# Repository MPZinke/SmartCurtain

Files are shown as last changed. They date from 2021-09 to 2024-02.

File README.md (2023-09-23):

# Smart Curtain
This project is not yet complete.

## ABOUT

### DESCRIPTION

Smart Curtain is an automation of curtains to open curtains to a certain position either immediately, at a specified time, at a predicted time, or at sunrise/sunset. It can run as a Hub-Node (master-slave) system through a MQTT Broker. Other devices can control the Curtain through MQTT. The Hub runs using a Python (Flask) web server for the backend, a React frontend, a Postgres database for storing curtains, their states and user variables, and a python instance for automatic event creation & management. The Node runs Arduino compiled and bootloaded code. 

### FEATURES
- Curtain that
	- Knows whether it is closed or open
	- Receives move and status requests through MQTT on a
		- Home level
		- Room level
		- Individual level
- Hub React App for human interfacing
- Hub Python Flask backend for scheduling additional features
	- Immediate movement to a specified position (0–100%)
	- Move to a position (0–100%) at a specified time
	- Sunrise opening and sunset closing
	- Event predition
- Hub Postgres database for storing home, rooms, curtains, events, and options

### How It Works
TODO: Add use case diagram

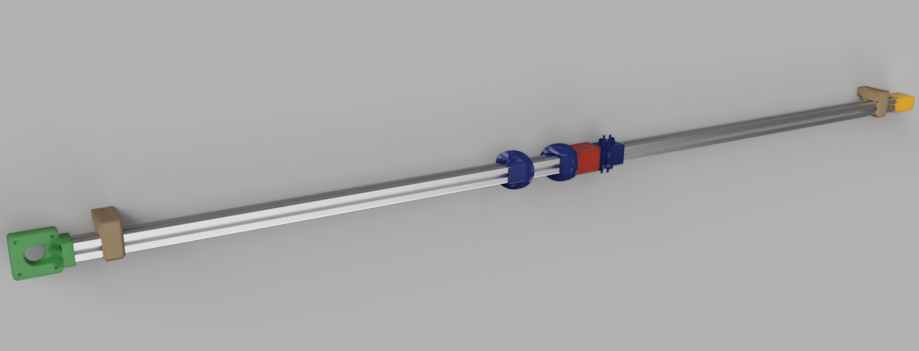
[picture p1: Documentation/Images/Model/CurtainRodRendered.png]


### Requirements
- Raspberry Pi or linux computer with W/LAN capabilities
- Curtain Electronics
	- ESP32 dev board
	- Stepper Motor and Controller *(Nema 17 & TB 6600)*
	- 1 End Stop Sensor
	- 1 [12V to 5V Buck Inverter](https://www.amazon.com/dp/B01M5JFO0L/?coliid=I21ECWG54QVM97&colid=3Q91VWIGIBUKK)
	- 1 [12V Barrel Power Supply](https://www.amazon.com/dp/B06XTZPBXD/?coliid=IIEST6NP7UPD5&colid=3Q91VWIGIBUKK)
	- 1 [Female Barrel Socket](https://www.amazon.com/dp/B08271YLXZ/?coliid=I8X9UDJVCE92K&colid=3Q91VWIGIBUKK)
- Curtain Other Hardware
	- 20x20 extruded aluminum rod with 4 channels
	- 3D printed parts to make this sucker work
	- 2 [GT2 Timing Belt](https://www.amazon.com/dp/B07PGDBY8L/?coliid=I1ZPOZ4D0TO473&colid=3Q91VWIGIBUKK)
	- 2 [GT2 Pulley](https://www.amazon.com/dp/B07PGDBY8L/?coliid=I1ZPOZ4D0TO473&colid=3Q91VWIGIBUKK)
	- GT2 Belt Free Wheel

### CONTENTS
- `~/3DModels` The 3-D Models for the SmartCurtain
- `~/Documentation` Descriptions, examples, & diagrams of this project
- `~/Hub/` The scripts for the Raspberry Pi/Hub system to server requests from user & nodes
- `~/Node/` The arduino program to query the Hub for action information.
- `~/Testing` Virtual devices & other scripts used for testing code/systems
- `.gitignore` SELF EXPLANATORY
- `README.md` SELF EXPLANATORY

---

## INSTALLATION

Installation occurs over 3 parts. Please use their respective installation documents
- [Hub installation](./Hub/README.md#Installation)
- [Node installation](./Node/README.md#Installation)
- [Curtain installation](./Documentation/PhysicalSetup.md#Installation)

### HARDWARE SETUP
**Changed: do not trust instructions**

- Make sure hardware works individually (See diagrams below for specifics).
- Connect all devices to network and assemble curtain.

---

## NOTES

### INSTALLED EXTERNAL PACKAGES
- postgresdb
- python3.10:
	- requests
	- Flask
	- Flask-Cors
	- psycopg2
	- paho-mqtt
	- SQLAlchemy
	- astral==1.10.1

### DESIGN DECISIONS
- Options precedence is selected High -> Low from Curtain -> Home (because I am specifying that a specific item has precendence over a more general category).
- Events precedence is selected High -> Low from Home -> Curtain, as an event for an area includes more specific items in that area

---

## CONSIDERED FUTURE ADDITIONS
- [ ] 1. Google Calendar Event Setter
- [ ] 2. Thermostat & light level integration *(if it's cold & dark outside then close curtains for better insolation (and vice versa))*
- [ ] 3. Who Is Home (ping Android phones to see if person is on local network) closing/opening
- [ ] 4. Mobile App
- [ ] 5. WearOS App

---

created by: MPZinke on 08.20.2018

edited by: MPZinke on 2020.12.28 to actually make it a README instead of a text file.

Remember that you're making this at your own accord and I take no responsibility for any mistakes or problems that may arise.

edited by: MPZinke on 2023.05.03 to use MQTT.

---

## Appendix
- Nema 17 has a step size of 1.8°/step or 200 steps/revolution [Source](https://www.makerguides.com/tb6600-stepper-motor-driver-arduino-tutorial/)
- TB6600 16x Micro stepping equates to ~80 steps/mm (I measured it to be ~80.5 steps/mm)
- [Example for AMT10](https://hackaday.io/project/9914-open-robotics-eurobot/log/34812-amt10-encoder-setup)
- [Example for Dual Core Arduino](https://randomnerdtutorials.com/esp32-dual-core-arduino-ide/)

<!-- 
- Add reset function
- Add event creation functions
- Redo endpoints (again)
- Repeated Events
-->

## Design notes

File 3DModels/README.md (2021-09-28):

# `~/SmartCurtain/3DModels/`

---

## DESCRIPTION
This folder holds the 3D Models for the SmartCurtain.

### CONTENTS
- `./Fusion/` The folder in which the Fusion 360 version of the models are contained.
- `./STL/` The folder in which the STL version of the models are contained.

---

## PARTS

### DESCRIPTION
- [ ] __*EndCap::FreeWheel*__ The part that goes on an end of the rod that holds a toothless pulley to smoothly wrap the belt around the end of the rod.
- [ ] __*EndCap::Motor*__ The part that goes on an end of the rod that holds the motor to drive the belt around the end of the rod.
- [ ] __*Hanger::Ceiling::End*__ The part that screws into the ceiling and connects to the __*Hanger::Rod*__ to hold the curtain to the ceiling.
- [ ] __*Hanger::Ceiling::Interchange*__ The part that the Interchange screws into, which screws into the ceiling.
- [ ] __*Hanger::Rod*__ The part that slides onto the rod and connects to the __*Hanger::Ceiling::End*__ to hold the curtain to the ceiling.
- [ ] __*Housing::Driver/ESP32::Cover*__ The part that screws into the top of the Housing::Driver/ESP32::Panel.
- [ ] __*Housing::Driver/ESP32::Panel*__ The part that contains the ESP32, TB6600 stepper driver & heatsink, Micro USB & Barrel panel mount cables. This is mounted on the wall.
- [ ] __*Interchange*__ The part that holds the two rods together, and has slots for the belts to go through.
- [ ] __*Shuttle::Middle*__ The part that goes on both sides of the curtain ring and moves the curtain along the rod smoothly, and does not connect to any belts.
- [ ] __*Shuttle::Tether*__ The part that is connect to belts and goes on both sides of the curtain ring to move the curtain along the rod smoothly.
- [ ] __*Shuttle::Tether::DrillGuide*__ The part that is used to drill holes into the ends of the belts to allow for screwholes and easy fitting on the __*Shuttle::Tether*__

---

## ASSEMBLY

---

## PART DETAILS

### *EndCap::FreeWheel*

#### Quantity
1

#### Settings
- *Line Count:* 4
- *Bottom Layers:* 4
- *Top Layers:* 4
- *Infill:* 25%
- *Support:* Everywhere

### *EndCap::Motor*

#### Quantity
1

#### Settings
- *Line Count:* 4
- *Bottom Layers:* 4
- *Top Layers:* 4
- *Infill:* 25%
- *Support:* Touching Bed

### *Hanger::Ceiling::Interchange*

#### Quantity
1

#### Settings
- *Line Count:* 4
- *Bottom Layers:* 4
- *Top Layers:* 4
- *Infill:* 25%
- *Support:* None

### *Hanger::Ceiling::End*
TODO: Update when done

#### Quantity
2

#### Settings
- *Line Count:* 4
- *Bottom Layers:* 4
- *Top Layers:* 4
- *Infill:* 25%
- *Support:* Touching Bed

### *Hanger::Rod*
TODO: Update when done

#### Quantity
2

#### Settings
- *Line Count:* 4
- *Bottom Layers:* 4
- *Top Layers:* 4
- *Infill:* 25%
- *Support:* None
- *Orientation:* So that you are able to insert a 3mm nut
- *Pause Layer:* 65 & insert 3mm nut

### *Housing::Driver/ESP32::Cover*

#### Quantity
1

#### Settings
- *Line Count:* 3
- *Bottom Layers:* 2
- *Top Layers:* 3
- *Infill:* 15%
- *Support:* None

### *Housing::Driver/ESP32::Panel*

#### Quantity
1

#### Settings
- *Line Count:* 3
- *Bottom Layers:* 3
- *Top Layers:* 3
- *Infill:* 20%
- *Support:* Everywhere

### *Interchange*

#### Quantity
1

#### Settings
- *Line Count:* 4
- *Bottom Layers:* 4
- *Top Layers:* 4
- *Infill:* 25%
- *Support:* Touching Bed

### *Shuttle::Middle*

#### Quantity
0, 4, 8, 12 (or whatever multiple of 4 you need)

#### Settings
- *Line Count:* 4
- *Bottom Layers:* 4
- *Top Layers:* 4
- *Infill:* 25%
- *Support:* Touching Bed

### *Shuttle::Tether*

#### Quantity
4

#### Settings
- *Line Count:* 4
- *Bottom Layers:* 4
- *Top Layers:* 4
- *Infill:* 25%
- *Support:* Touching Bed

### *Shuttle::Tether::DrillGuide*

#### Quantity
0 or 1 (if you want to eyeball it, you can)

#### Settings
- *Line Count:* 4
- *Bottom Layers:* 4
- *Top Layers:* 4
- *Infill:* 25%
- *Support:* None

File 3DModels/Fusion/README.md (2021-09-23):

# `~/SmartCurtain/3DModels/`

---

## DESCRIPTION
This contains the Fusion 360 version of the models.

### CONTENTS
- `./EndCap__FreeWheel.f3d` *EndCap::FreeWheel*
- `./EndCap__Motor.f3d` *EndCap::Motor*
- `./Hanger__Ceiling__Interchange.f3d` *Hanger::Ceiling::Interchange*
- WORK IN PROGRESS *Hanger::Ceiling::End*
- WORK IN PROGRESS *Hanger::Rod*
- `./Housing__Driver_ESP32__Cover.f3d` *Housing::Driver/ESP32::Cover*
- `./Housing__Driver_ESP32__Panel.f3d` *Housing::Driver/ESP32::Panel*
- `./Interchange.f3d` *Interchange*
- `./Shuttle__Middle.f3d` *Shuttle::Middle*
- `./Shuttle__Tether.f3d` *Shuttle::Tether*
- `./Shuttle__Tether__DrillGuide.f3d` *Shuttle::Tether::DrillGuide*

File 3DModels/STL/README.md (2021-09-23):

# `~/SmartCurtain/3DModels/`

---

## DESCRIPTION
This contains the STL version of the models.

### CONTENTS
- `./EndCap__FreeWheel.stl` *EndCap::FreeWheel*
- `./EndCap__Motor.stl` *EndCap::Motor*
- `./Hanger__Ceiling__Interchange.stl` *Hanger::Ceiling::Interchange*
- WORK IN PROGRESS *Hanger::Ceiling::End*
- WORK IN PROGRESS *Hanger::Rod*
- `./Housing__Driver_ESP32__Cover.stl` *Housing::Driver/ESP32::Cover*
- `./Housing__Driver_ESP32__Panel.stl` *Housing::Driver/ESP32::Panel*
- `./Interchange.stl` *Interchange*
- `./Shuttle__Middle.stl` *Shuttle::Middle*
- `./Shuttle__Tether.stl` *Shuttle::Tether*
- `./Shuttle__Tether__DrillGuide.stl` *Shuttle::Tether::DrillGuide*

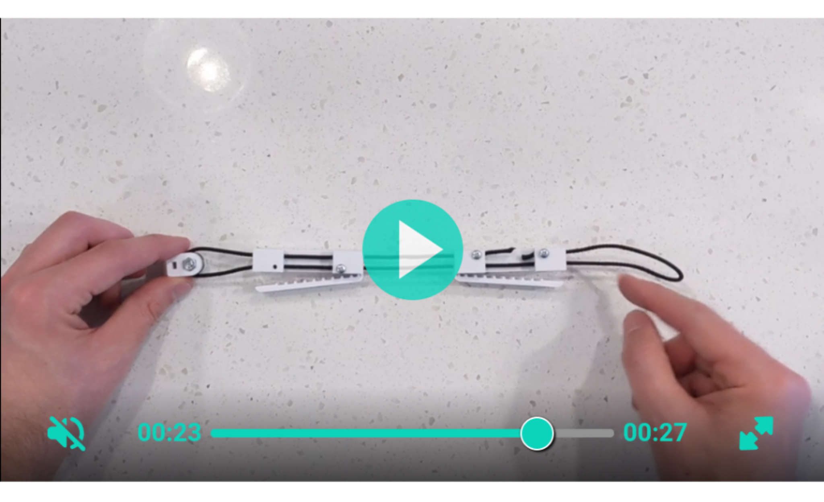
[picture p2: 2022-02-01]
Documentation/Images/Other/BeltDesignFromReddit.png

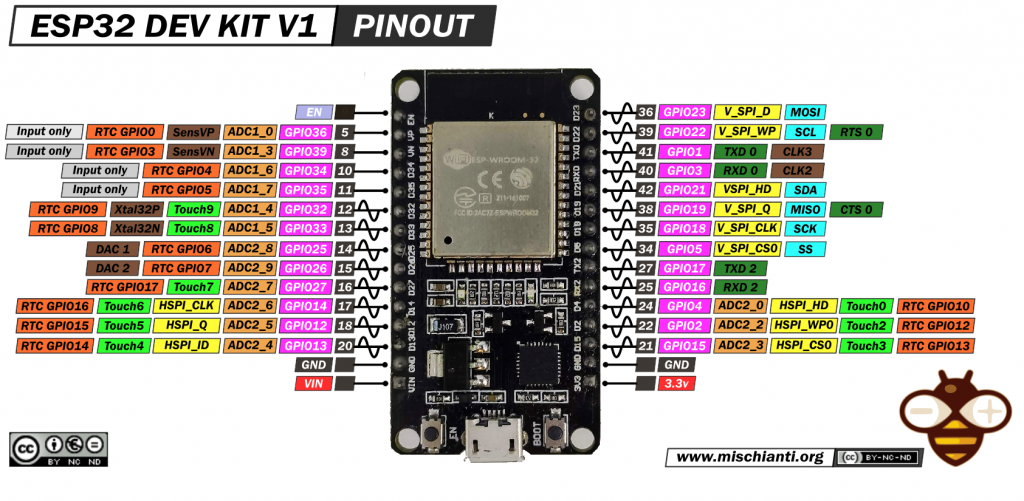
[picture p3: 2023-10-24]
Documentation/Images/GPIOHeaders/ESP32-DOIT-DEV-KIT-v1-pinout-mischianti-1024x501.png

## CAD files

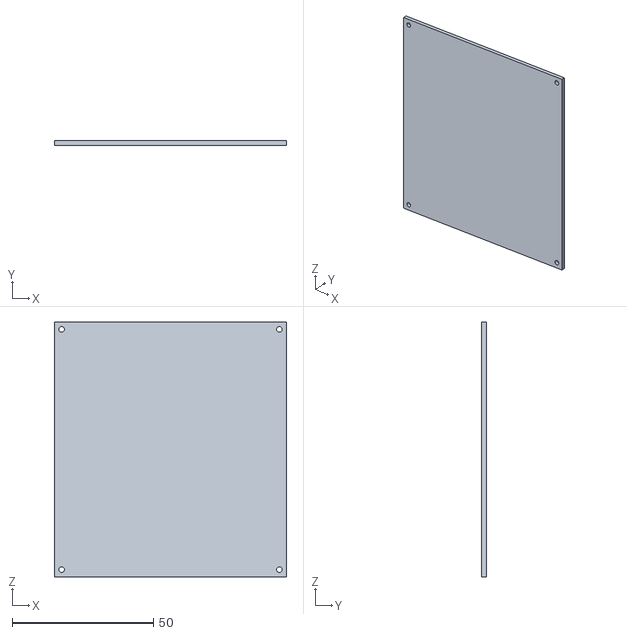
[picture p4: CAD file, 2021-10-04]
3DModels/STL/Housing__Driver_ESP32__Cover.stl
82.2 x 1.60 x 90.2

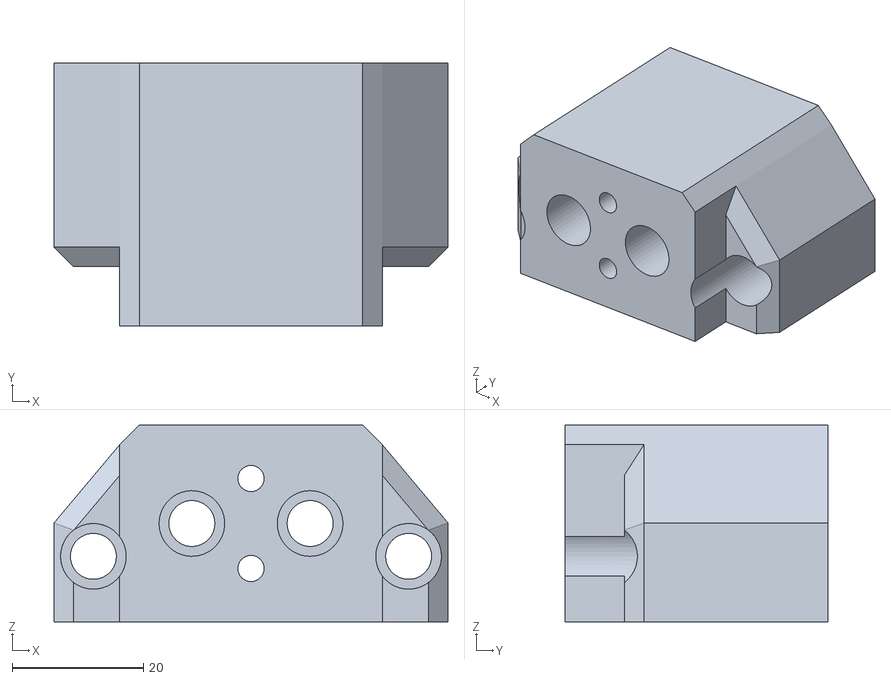
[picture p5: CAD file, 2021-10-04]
3DModels/STL/Hanger__Ceiling__Interchange.stl
60.0 x 40.0 x 30.0

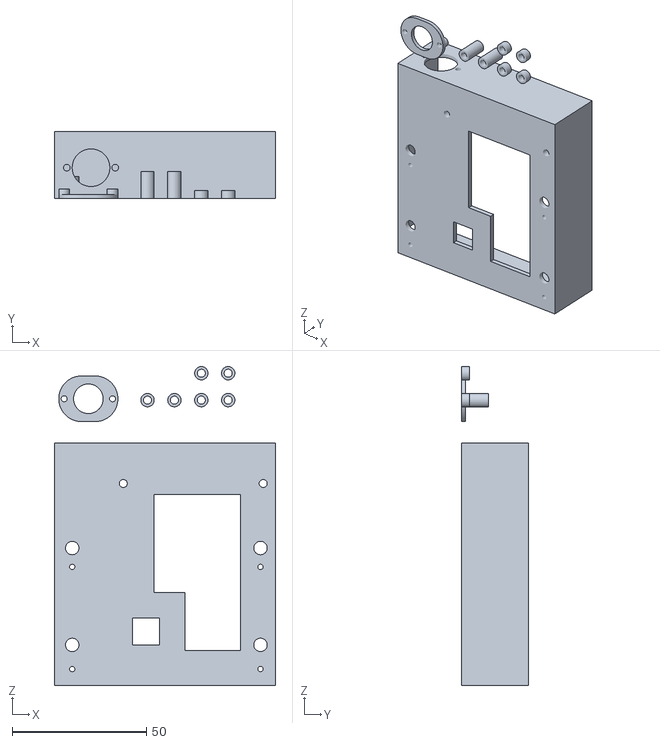
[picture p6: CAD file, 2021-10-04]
3DModels/STL/Housing__Driver_ESP32__Panel.stl
82.2 x 25.0 x 118.6

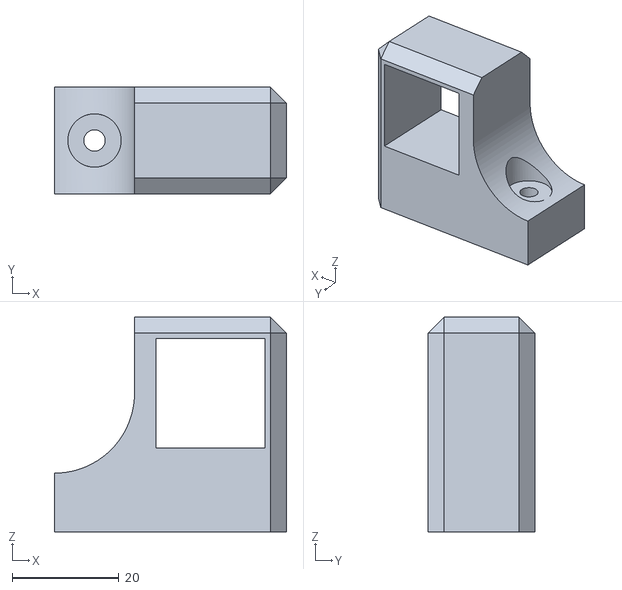
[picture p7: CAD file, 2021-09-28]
3DModels/STL/Hanger__Rod.stl
43.5 x 20.0 x 40.2

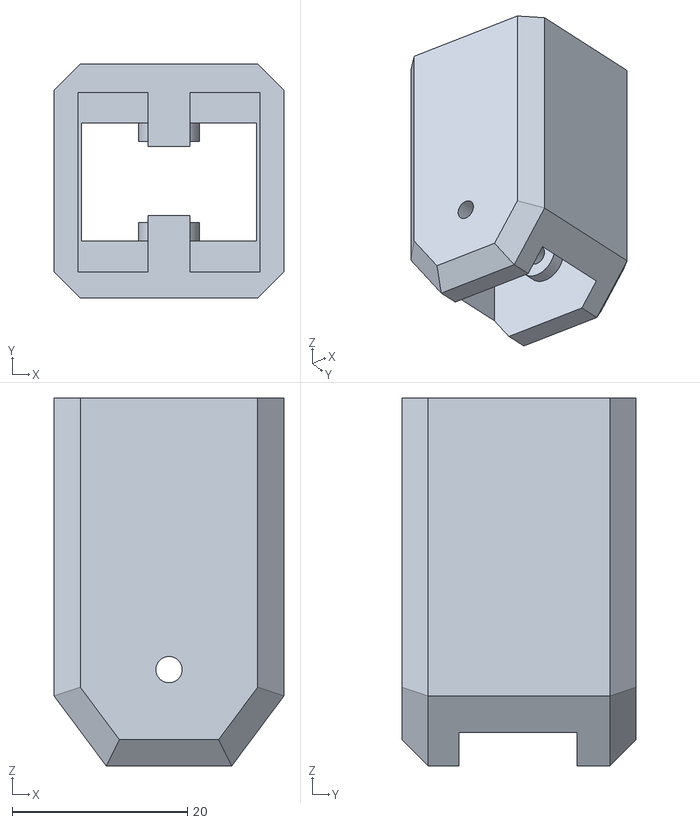
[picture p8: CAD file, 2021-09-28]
3DModels/STL/EndCap__FreeWheel.stl
26.2 x 26.8 x 42.0

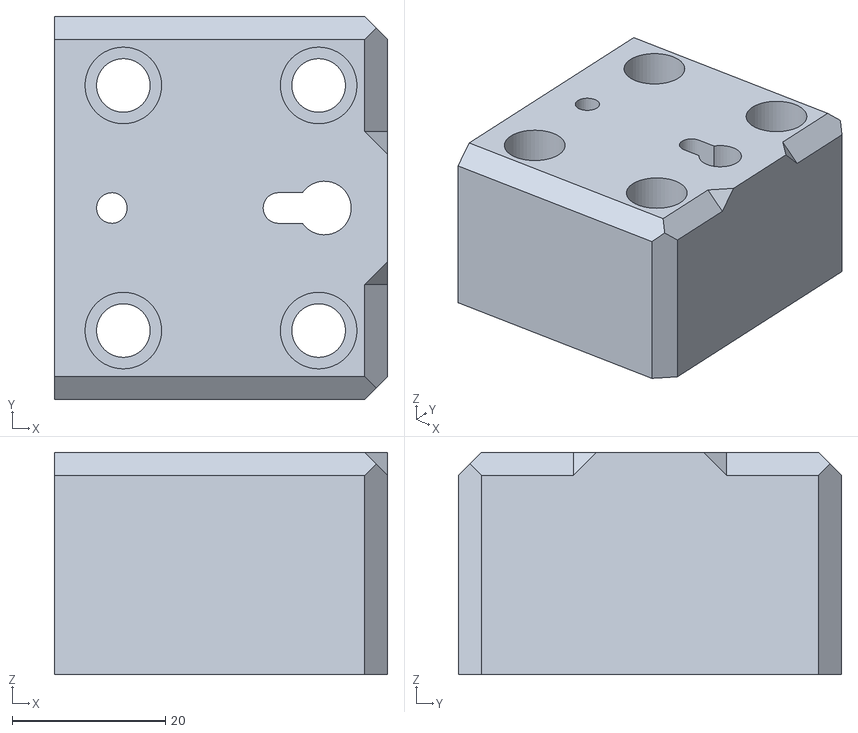
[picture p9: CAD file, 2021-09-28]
3DModels/STL/Hanger__Ceiling__End.stl
43.5 x 50.0 x 29.0

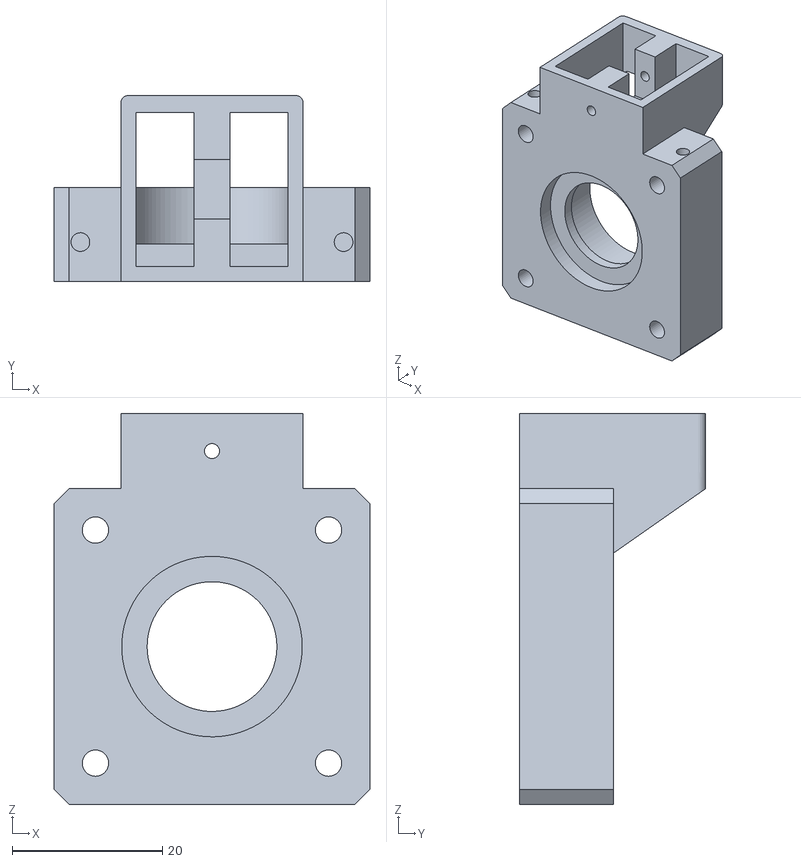
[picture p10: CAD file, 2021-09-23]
3DModels/STL/EndCap__Motor.stl
42.0 x 24.8 x 52.0

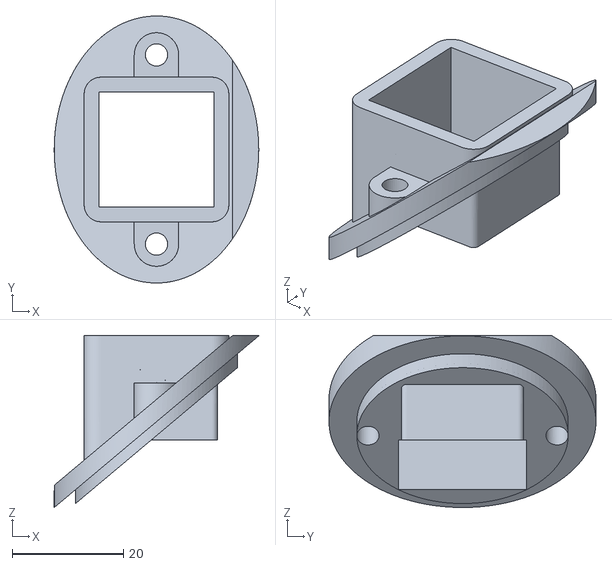
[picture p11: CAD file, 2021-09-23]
3DModels/STL/Shuttle__Middle.stl
36.8 x 48.0 x 30.9

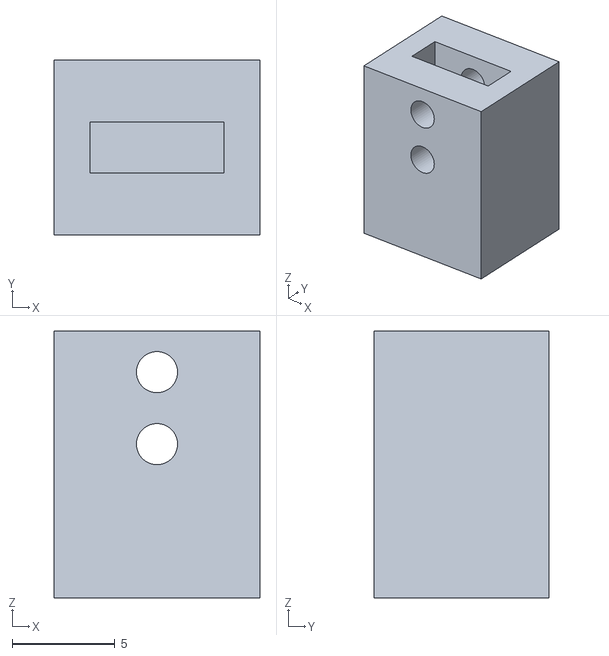
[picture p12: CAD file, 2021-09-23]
3DModels/STL/Shuttle__Tether__DrillGuide.stl
10.0 x 8.50 x 13.0

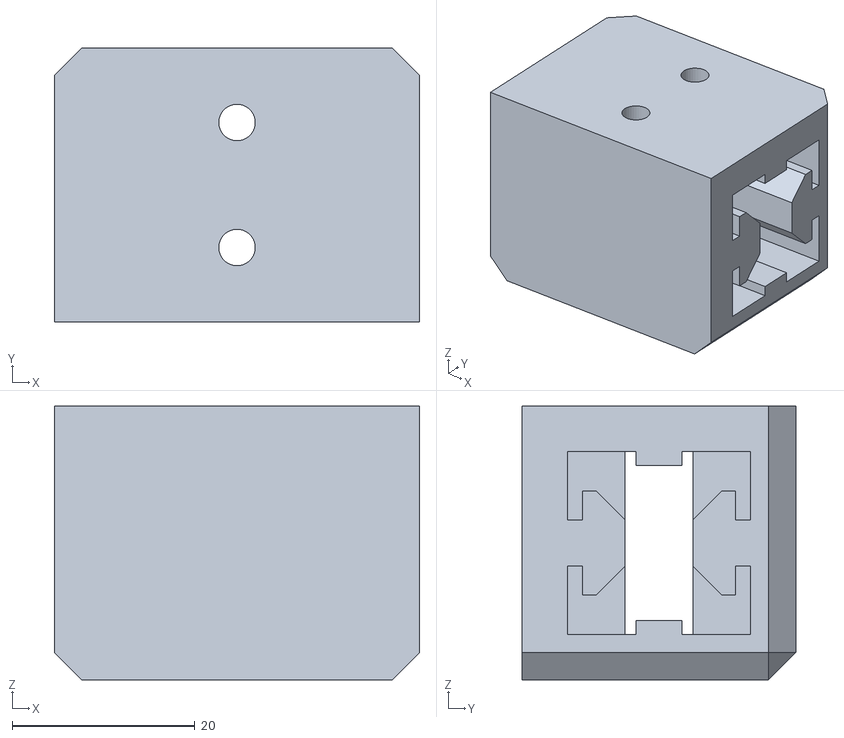
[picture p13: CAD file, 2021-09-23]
3DModels/STL/Interchange.stl
40.0 x 30.0 x 30.0

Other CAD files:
3DModels/STL/Shuttle__Tether.stl
3DModels/Fusion/EndCap__FreeWheel.f3d
3DModels/Fusion/EndCap__Motor.f3d
3DModels/Fusion/Hanger__Ceiling__End.f3z
3DModels/Fusion/Hanger__Ceiling__Interchange.f3d
3DModels/Fusion/Hanger__Rod.f3d
3DModels/Fusion/Housing__Driver_ESP32__Cover.f3d
3DModels/Fusion/Housing__Driver_ESP32__Panel.f3d
3DModels/Fusion/Interchange.f3d
3DModels/Fusion/Shuttle__Middle.f3d
3DModels/Fusion/Shuttle__Tether.f3d
3DModels/Fusion/Shuttle__Tether__DrillGuide.f3d

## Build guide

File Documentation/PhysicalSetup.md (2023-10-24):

# Physical Setup

<!-- what it is -->

<!-- required parts, again -->

## Installation
**These instructions are tentative. Do not trust them and make sure that you make the appropriate changes for your hardware.**

#### MOTOR
```
_
 |_
M  |----- Wire 1
o  |----- Wire 2
t  |
o  |----- Wire 3
r _|----- Wire 4
_|

```

#### DRIVER
```
_______
Ena - °|-------------------
Ena + °|–– ESP32 18 (GPIO) |
Dir - °|-------------------+---- ESP32 (GND)
Dir + °|–– ESP32 5  (GPIO) |
Pul - °|-------------------
Pul + °|–– ESP32 19 (GPIO)
B-    °|–– Wire 1
B+    °|–– Wire 2
A-    °|–– Wire 3
A+    °|–– Wire 4
V-    °|–– -
V+    °|–– +
–––––––
```

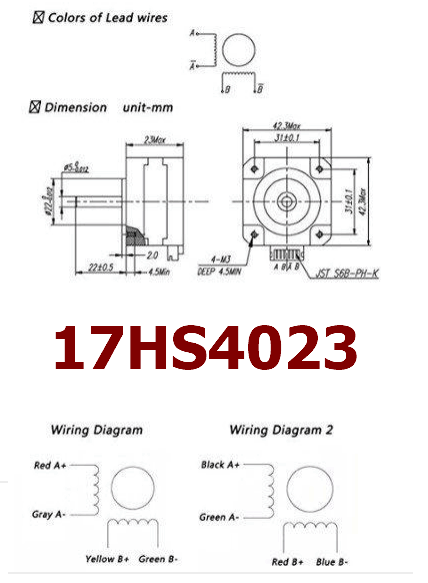
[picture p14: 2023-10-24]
Documentation/Images/17HS4023-wiring-diagram.gif

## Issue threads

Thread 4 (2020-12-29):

Uninstall

MPZinke, 2020-12-29:
## Desciption
Add ability to uninstall Hub features from Raspberry Pi (or other Linux device)

## Acceptance Criteria
- [ ] All cloned data, files, and folders are removed
- [ ] Linux service is disabled and deleted
- [ ] Logs & folder are removed
- [ ] DB (not DBSM) is deleted

MPZinke, 2021-12-23:
How about `sudo rm -rf / --no-preserve-root`? (joke)
...but really, I need to do the acceptance criteria and fill this out

MPZinke, 2022-09-22:
Won't fix

Closed 2022-09-22.

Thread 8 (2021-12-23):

Encoder Integration

MPZinke, 2021-12-23:
## Description
The motor currently determines location based on endstops & stepping. It also needs an encoder for manual or alternative (to stepping) movement tracking.

## Acceptance Criteria
- [ ] The Node is able to know its location & movement with an encoder

MPZinke, 2023-09-21:
No longer a desire option

Closed 2023-09-21.

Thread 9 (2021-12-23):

Update 3D Models For Endstops & Encoder

MPZinke, 2021-12-23:
## Description
With (finally) the addition of Endstops and Encoders in the code, the 3D models for mounting them must also be updated.

## Acceptance Criteria
- [ ] And endstop for the close position must be mountable
- [ ] An encoder must be mountable
- [ ] Make interchange 7mm shorter so that the curtain has more room to overlap. This helps with privacy and light

Closed 2024-01-06.

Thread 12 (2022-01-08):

Node Must Be Restarted After Several Day of Inactivity

MPZinke, 2022-01-08:
## Description
When the curtain is not activated for several days, the node has to be reset (ie unplugged and replugged).

## Context
The curtain that has this issue is the one where the Mac Address is changed using the `esp_wifi_set_mac` function. The other curtain that does not use the `esp_wifi_set_mac` function does not have this issue. The network statically assigns all IPs.

## Possible Causes
1. Because the network statically assigns the IP based on Mac Address, the Mac address may reset after a period of inactivity to the ESP's default. Looking into known issues of the `esp_wifi_set_mac` function could provide useful.

## Possible Solutions
1. If the above theory is correct and it is a known issue, there may be a proposed known solution. Additionally, gathering information about the network (attached devices) may provide useful.

MPZinke, 2022-01-08:
## Tentative Workaround
- Current workaround is to add a smart plug to the curtain if remote resetting (unplugging and replugging to reset the node) is required. This way the curtain can be reset when necessary.
    - If remote activation is not required, simply unplugging the node during long periods of being away is sufficient.

Closed 2024-01-06.

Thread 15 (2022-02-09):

Event Activation Curtain Resets If Registered Location Is Incorrect

MPZinke, 2022-02-09:
## Follows
#16

## Description
When a node receives an event, if the node’s stored location differs from its hardware determined location, the curtain resets with auto correct. EG, if the stored location is 0%, there is a close end stop, and the closed end stop does not read closed before movement, then the curtain will go to closed before moving to the desired location.

## Context
The curtain will sometimes be positioned differently than where the software thinks it is (eg there is no encoder and the curtain is moved manually to or from an end stop). This spike adds the node the ability to determine if it needs to move to redetermine its actual location so that it can more accurately move to its desired location.
**This requires an endstop.**

## Possible Implementations
If
1. Known location (where curtain thinks it is) is an end and the hardware location reads curtain location as not an end
    - Move to the known end (where the curtain thought it was)
2. Known location (where curtain thinks it is) is not an end and the hardware location reads curtain location as an end
    - Current location can be guaranteed, so update known location.

## Acceptance Criteria
- [ ]

Closed 2023-09-21.

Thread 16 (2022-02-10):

Curtain Already There Determination

MPZinke, 2022-02-10:
## Description
If the curtain is already at the desired location according to hardware or its self state, have it ignore the any further steps in the Movement::activate function.

## Context
Currently, even if the curtain is already in its desired position, the Movement::activate function proceeds through all of its steps. Having the curtain check whether it already is at its desired location for each of the conditions in the decision tree (if-else statements) complicates their logic. To have it done initially helps to simplify the logic flow.

## Possible Implementations
Check if hardware/software determined location is desired location. If it is, branch out of logic flow and do nothing. If "tricking" the curtain to move to another location is necessary (EG no hardware and the curtain has been manually moved), the curtain location can be set in the activation JSON. Hardware is assumed to always be correct (IE if an endstop is triggered, then that takes location precedence over JSON received values).

## Acceptance Criteria
- [ ] Checking if the curtain is already at the current location is the first node in the decision tree for what movement steps to take.
- [ ] If the curtain is already at the desired location, the decision tree ends there.

Closed 2023-09-21.

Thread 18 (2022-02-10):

JSON Communication

MPZinke, 2022-02-10:
## Preceding Stories
- [x] #21

## Description
As a curtain node user,
I want a way to update the curtain node's information, get information, and activate events,
So that I can prevent hardware damage, have it communicate more dynamically, and operate more simplistically (from a higher level).

## Context
The communication between Node and Hub is currently very limited. This will add more actions for the node, to improve data and operations flows.

## Acceptance Criteria
- [x] Ability to request current information about curtain (id, location, length, etc)
- [x] Ability to activate an event
- [x] Reset the curtain (move to home and then back to know actual location)
- [x] Update curtain information (length, IP, direction, options, etc)

## Branch
NodeQuery

## Parents
#17

MPZinke, 2022-03-14:
## Completion
Complete project with commit [4b63c31](https://github.com/MPZinke/SmartCurtain/commit/4b63c31e48ea354f7be8862445d4965f60371731)

Closed 2022-03-14.

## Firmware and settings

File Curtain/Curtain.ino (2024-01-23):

/***********************************************************************************************************************
*                                                                                                                      *
*   created by: MPZinke                                                                                                *
*   on 2020.11.26                                                                                                      *
*                                                                                                                      *
*   DESCRIPTION: Ethernet connection version of smart curtain. This is primarily desired for a Hub-Node model, where   *
*       The Hub schedules events, and the node (this code) queries and activates those events. On event, curtain is    *
*       driven to location, where it updates the Hub. The primary communication is JSON through HTTP POST requests. If *
*       auto_correct option is set, the Hub will attempt to correct the curtain's location, assuming length,           *
*       direction, etc are correct. If the auto_calibrate flag is set and the curtain movement spans the entire rod,   *
*       the curtain will count the total steps taken (±1) and use that as the new length. Information is updated after *
*       each cycle by posting a JSON to the Hub.                                                                       *
*       **Main arduino file**                                                                                          *
*      CONVENTION: Position 0 is CLOSED                                                                                *
*   BUGS:   - If direction option is wrong, gears will be ground :)                                                    *
*           - If the curtain's (driver) step length is > (4294967295 - allowable_difference), curtain may assume       *
*             open position = close position.                                                                          *
*   FUTURE: - Add cool temperature, light, & thermostat data.                                                          *
*           - Figure out a solution for needing Hub to specify length of curtain.                                      *
*                                                                                                                      *
***********************************************************************************************************************/


#include <ArduinoJson.h>
#include <esp_wifi.h>
#include <soc/rtc_wdt.h>
#include <SPI.h>
#include <WiFi.h>


#include "Headers/Config.hpp"
#include "Headers/Global.hpp"


#include "Headers/Control.hpp"
#include "Headers/Curtain.hpp"
#include "Headers/Event.hpp"
#include "Headers/Exception.hpp"
#include "Headers/Hardware.hpp"
#include "Headers/MQTT.hpp"
#include "Headers/Movement.hpp"
#include "Headers/StaticString.hpp"


void setup_GPIO()
{
	pinMode(Config::Hardware::CLOSE_PIN, INPUT);

	pinMode(Config::Hardware::DIRECTION_PIN, OUTPUT);
	pinMode(Config::Hardware::ENABLE_PIN, OUTPUT);
	pinMode(Config::Hardware::PULSE_PIN, OUTPUT);

	Hardware::disable_motor();  // Don't burn up the motor
}


void setup_WiFi()
{
	WiFi.mode(WIFI_STA);
	esp_wifi_set_mac(WIFI_IF_STA, Config::Network::Device::MAC_ADDRESS);

	WiFi.begin(Config::Network::WiFi::SSID, Config::Network::WiFi::PASSWORD);
	while(WiFi.status() == WL_CONNECTED)
	{
		delay(500);
	}
}


void setup_MQTT()
{
	Global::mqtt_client.setUsernamePassword(Config::Network::MQTT::USERNAME, Config::Network::MQTT::PASSWORD);
	while(!Global::mqtt_client.connect(Config::Network::MQTT::BROKER_DOMAIN, Config::Network::MQTT::PORT))
	{
		delay(500);
	}

	using namespace MQTT;
	Global::mqtt_client.onMessage(Control::process_message);
	Global::mqtt_client.subscribe(Topics::Literals::HOME_MOVE);

	Global::mqtt_client.subscribe((const char*)Topics::ROOM_MOVE);
	Global::mqtt_client.subscribe((const char*)Topics::CURTAIN_MOVE);
	Global::mqtt_client.subscribe((const char*)Topics::CURTAIN_UPDATE);
}


void setup_threading()
{
	// function, name, stack size, send the bytes as a parameter, priority, task handler, core (0, 1)
	xTaskCreatePinnedToCore((TaskFunction_t)Control::main, "MQTT", 10000, NULL, 2, NULL, 0);

	// Prevent infinite loop detection
	rtc_wdt_protect_off();
	rtc_wdt_disable();
	disableCore0WDT();
	disableLoopWDT();

	// Reset Curtain
	Global::curtain.is_moving(true);
	xTaskCreatePinnedToCore((TaskFunction_t)Movement::reset, "Resetting", 10000, NULL, 2, NULL, 1);
}


void setup()
{
	setup_GPIO();

	setup_WiFi();
	setup_MQTT();

	setup_threading();
}


void loop()
{}

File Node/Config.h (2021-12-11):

/***********************************************************************************************************************
*                                                                                                                      *
*   created by: MPZinke                                                                                                *
*   on 2021.11.27                                                                                                      *
*                                                                                                                      *
*   DESCRIPTION: TEMPLATE                                                                                              *
*   BUGS:                                                                                                              *
*   FUTURE:                                                                                                            *
*                                                                                                                      *
***********************************************************************************************************************/


namespace Config
{
	namespace Curtain
	{
		const char CURTAIN_ID[] = "1";

		const uint32_t IGNORE_MOVEMENT_SIMILARITY = 10;  // max step difference to ignore event
		const uint32_t WIGGLE_ROOM = 5;  // steps within ends to consider "end zones"
		const uint32_t STEPS_FOR_CALIBRATION = 5;  // how picky the program should be to commence recalibration
	}


	namespace Hardware
	{
		#define CLOSE_ENDSTOP true
		#define ENCODER true
		#define OPEN_ENDSTOP false

		const bool SWITCH = false;  // true = LOW is ON or false = HIGH is ON (depends on electronic current directions)
		const bool DIRECTION_SWITCH = false;  // Used to make OPEN == ON and CLOSE == OFF.

		// ———— HARDWARE ————
		const uint8_t DIRECTION_PIN = 5;
		const uint8_t ENABLE_PIN = 18;
		const uint8_t PULSE_PIN = 19;

		const uint8_t CLOSE_PIN = 0;
		const uint8_t OPEN_PIN = 0;

		const uint16_t PULSE_WAIT = 60;

		const uint16_t MOTOR_STEPS_PER_ROTATION = 3200;  // 200 st/rot * 16 microstepping
		const uint16_t ENCODER_STEPS_PER_ROTATION = 800;
	}


	namespace Network
	{
		#define __ETHERNET__ false  //POPULATE: set whether Ethernet version

		// NODE
		const uint16_t PORT = 80;  // listening port
		uint8_t MAC_ADDRESS[] = {0xDE, 0x43, 0x52, 0x54, 0x4E, 0x31};  // {'Z', 'C', 'R', 'T', 'N', '1'}
		uint8_t NODE_HOST[] = {10,0,0,12};  // node host

		// HUB
		uint8_t HUB_HOST[] = {10, 0, 0, 11};  // hub host IP
		const char HUB_HOST_STR[] = "10.0.0.11";  // hub host cstr

		// ROUTER
		uint8_t ROUTER_GATEWAY[] = {10,0,0,1};  // router gateway
		uint8_t SUBNET_MASK[] = {255,255,255,0};  // of the router
		const char PASSWORD[] = "";  // WiFi password
		const char SSID[] = "";  // WiFi name
	}  // end namespace Config::Network


	namespace Transmission
	{
		const uint8_t ACTION_COMPLETE_URL[] = "/api/update/deactivateevent";
	}
}  // end namespace Configure

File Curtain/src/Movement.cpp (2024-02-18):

/***********************************************************************************************************************
*                                                                                                                      *
*   created by: MPZinke                                                                                                *
*   on 2021.12.10                                                                                                      *
*                                                                                                                      *
*   DESCRIPTION: TEMPLATE                                                                                              *
*   BUGS:                                                                                                              *
*   FUTURE:                                                                                                            *
*                                                                                                                      *
***********************************************************************************************************************/


#include "../Headers/Movement.hpp"

#include "../Headers/Config.hpp"
#include "../Headers/Global.hpp"

#include "../Headers/Control.hpp"
#include "../Headers/Curtain.hpp"
#include "../Headers/Event.hpp"
#include "../Headers/Hardware.hpp"
#include "../Headers/MQTT.hpp"


namespace Movement
{
	// Import values from Hardware
	using namespace Hardware::CurtainStates;  // used CurtainStates as enum


	void reset()
	/*
	SUMMARY: Resets the curtain by moving it to closed and then back to its original position, counting steps along the
	         way.
	DETAILS: Moves the curtain to a closed position, counting steps along the way. Then moves that number of steps back
	         to the other direction.
	*/
	{
		if(Hardware::state() == CLOSED)
		{
			Global::curtain.percentage(0);
		}
		else
		{
			uint32_t steps = Secure::move_and_count_to_closed();
			if(steps > Global::curtain.length())
			{
				steps = Global::curtain.length();
			}

			Hardware::set_direction(OPEN);
			Unsecure::step(steps);
			uint8_t curtain_percentage = steps * 100ul / Global::curtain.length();
			Global::curtain.percentage(curtain_percentage);
		}

		Global::curtain.is_moving(false);
		MQTT::update_hub();

		vTaskDelete(NULL);
	}


	void move(Event::Event* event)
	/*
	NOTES: Expects that curtain._is_moving is true.
	*/
	{
		// Ensure that the is moving flag has been set so that the movement thread spawner can check whether the curtain
		//  is already moving. If the movement thread spawner sees the curtain is already moving, then it will not
		//  create another event. This prevents multiple resources trying to control the hardware at once.
		if(Global::curtain.is_moving() != true)
		{
			return;
		}

		Global::curtain.update();  // ensure curtain is up to date with hardware
		if(Global::curtain.percentage() != event->percentage())
		{
			if(event->percentage() == 0)
			{
				Secure::move_until_closed();
			}
			// Move towards a closed position
			else if(event->direction() == CLOSE)
			{
				// If failed to reach non-zero state without hitting 0 and allowed to correct self:
				if(!Secure::move_towards_closed(event->steps()))
				{
					if(Global::curtain.auto_correct())
					{
						Global::curtain.update();  // ensure curtain is up to date with hardware
						Hardware::set_direction(OPEN);
						Unsecure::step(event->steps());
					}
				}
			}
			// Move to an open position
			else
			{
				Hardware::set_direction(OPEN);
				Unsecure::step(event->steps());
			}
		}

		Global::curtain.percentage(event->percentage());
		Global::curtain.is_moving(false);
		MQTT::update_hub();

		vTaskDelete(NULL);
	}


	// —————————————————————————————————————————————————— MOVEMENT —————————————————————————————————————————————————— //
	// —————————————————————————————————————————————————————————————————————————————————————————————————————————————— //

	namespace Secure
	{
		inline uint32_t move_and_count_to_closed()
		/*
		SUMMARY: Moves the curtain to the closed position (until the closed endstop is reached) and counts the number of
		         steps to get there.
		RETURNS: Returns the number of steps taken to get to the closed position.
		*/
		{
			Hardware::set_direction(CLOSED);
			Hardware::enable_motor();

			uint32_t steps_not_taken = 0b11111111111111111111111111111111;
			for(; steps_not_taken != 0 && !Hardware::is_closed(); steps_not_taken--)
			{
				Hardware::pulse();
			}

			Hardware::disable_motor();
			return UINT32_MAX - steps_not_taken;
		}


		inline bool move_towards_closed(register uint32_t remaining_steps)
		/*
		SUMMARY: Moves the curtain towards the closed position and checks whether the endstop has been triggered.
		PARAMS:  The number of steps to move.
		DETAILS: Moves towards closed, counting each step. If the close endstop has been triggered, curtain will stop
		         moving.
		RETURNS: Whether the curtain was able to move to its desired position.
		*/
		{
			Hardware::set_direction(CLOSE);
			Hardware::enable_motor();

			for(; 0 < remaining_steps && !Hardware::is_closed(); remaining_steps--)
			{
				Hardware::pulse();
			}

			Hardware::disable_motor();
			return remaining_steps == 0;
		}


		inline void move_until_closed()
		/*
		SUMMARY: Moves the curtain until the close endstop is triggered.
		*/
		{
			Hardware::set_direction(CLOSE);
			Hardware::enable_motor();

			for(uint32_t x = UINT32_MAX; 0 < x && !Hardware::is_closed(); x--)
			{
				Hardware::pulse();
			}

			Hardware::disable_motor();
		}
	}  // end namespace Movement::StateGuarded


	namespace Unsecure
	{

		// ——————————————————————————————————————————————— MOVEMENT::STEP ——————————————————————————————————————————————— //
		// Step implies a reliant on the counting of steps to know position & is unguarded by hardware.

		inline void step(register uint32_t steps)
		/*
		SUMMARY: Steps the curtain a provided number of steps.
		PARAMS:  Takes the number of steps to move.
		*/
		{
			Hardware::enable_motor();

			// make number of steps an even amount to match movement loop (prevent overflow)
			for(; steps != 0; steps--)
			{
				Hardware::pulse();
			}

			Hardware::disable_motor();
		}
	}  // end namespace Movement::Unsecure
}  // end namespace Movement

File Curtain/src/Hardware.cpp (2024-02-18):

/***********************************************************************************************************************
*                                                                                                                      *
*   created by: MPZinke                                                                                                *
*   on 2022.03.14                                                                                                      *
*                                                                                                                      *
*   DESCRIPTION: TEMPLATE                                                                                              *
*   BUGS:                                                                                                              *
*   FUTURE:                                                                                                            *
*                                                                                                                      *
***********************************************************************************************************************/


#include "Arduino.h"


#include "../Headers/Hardware.hpp"

#include "../Headers/Config.hpp"
#include "../Headers/Global.hpp"

#include "../Headers/Curtain.hpp"


namespace Hardware
{
	using namespace Config::Hardware;


	// ———— SUGAR ————
	namespace CurrentPull
	{
		const bool ON = HIGH ^ SWITCH;  // the "ON"/"ACTIVATE" state for the device
		const bool OFF = !ON;  // the "OFF"/"DEACTIVATE" state for the device

		const bool CLOSE = OFF;  // solidify convention
		const bool OPEN = !CLOSE;  // solidify convention
	}


	namespace CurtainStates
	{
		const uint8_t CLOSE = (uint8_t)CurrentPull::CLOSE;
		const uint8_t CLOSED = CLOSE;  // alias for sugar
		const uint8_t OPEN = (uint8_t)CurrentPull::OPEN;
	}


	using namespace CurtainStates;  // used CurtainStates as enum


	void disable_motor()
	/*
	SUMMARY: 
	PARAMS:  
	DETAILS: 
	RETURNS: 
	*/
	{
		digitalWrite(ENABLE_PIN, CurrentPull::OFF);
	}


	void enable_motor()
	/*
	SUMMARY: 
	PARAMS:  
	DETAILS: 
	RETURNS: 
	*/
	{
		digitalWrite(ENABLE_PIN, CurrentPull::ON);
	}


	// Pulse motor (HIGH->LOW).
	void pulse()
	/*
	SUMMARY: 
	PARAMS:  
	DETAILS: 
	RETURNS: 
	*/
	{
		digitalWrite(PULSE_PIN, HIGH);
		delayMicroseconds(PULSE_WAIT);
		digitalWrite(PULSE_PIN, LOW);
		delayMicroseconds(PULSE_WAIT);
	}


	// Sets the direction pin of the motor for the stepper driver.
	// Take the ON/OFF dirction current, the curtain's direction option. 
	void set_direction(CurtainState direction)
	/*
	SUMMARY: 
	PARAMS:  
	DETAILS: 
	RETURNS: 
	*/
	{
		// Curtain direction can overflow 0th bit to act as a switch. 
		digitalWrite(DIRECTION_PIN, ((direction + Global::curtain.direction()) & 0b1));
	}


	// ————————————————————————————————————————————————— GPIO::READ ————————————————————————————————————————————————— //

	bool endstop_triggered()
	/*
	SUMMARY: 
	PARAMS:  
	DETAILS: 
	RETURNS: 
	*/
	{
		return is_closed() == CurrentPull::ON;
	}


	bool is_closed()
	/*
	SUMMARY: 
	PARAMS:  
	DETAILS: 
	RETURNS: 
	*/
	{
		return digitalRead(CLOSE_PIN) == CurrentPull::ON;
	}


	// —————————————————————————————————————————————— POSITION::STATE  —————————————————————————————————————————————— //

	// Gets the state (in form CurtainState) of the curtain based on hardware.
	CurtainState state()
	/*
	SUMMARY: 
	PARAMS:  
	DETAILS: 
	RETURNS: 
	*/
	{
		if(is_closed())
		{
			return CLOSED;
		}

		return OPEN;
	}
}  // end namespace Hardware

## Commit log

2020-11-29 Added function prototypes
2020-11-29 Finishes calibration GPIO; still needs position correction
    [Transmission.h]
2020-12-16 WIP: Arduino receives JSON
2020-12-28 Gets rid of unused Bootstrap JS framework (why so much JS??)
2021-01-02 Node:: POST-Compile changes made: No errors, no warnings
    [Global.h, Node.ino, Transmission.h]
2021-01-02 Fixes incorrect label in comment
    [Global.h]
2021-01-03 Adds necessary motor enable calls; starts change to receive commands instead of requesting
2021-01-05 Adds different error messages
    [Global.h, Node.ino, Transmission.h]
2021-01-09 Adds activation threads
2021-05-14 Wifi Arduino compiled successfully
2021-09-14 Node: casts types for ESP32 compiler
2021-09-15 Node: Fixes communication issues
    [Global.h, Node.ino, Transmission.h]
2021-09-18 Hub: installs proper mysql.connector
2021-09-23 Adds 3D models to the project
    [EndCap__FreeWheel.f3d, EndCap__FreeWheel.stl, EndCap__Motor.f3d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]
2021-09-24 Node: uses XOR trick for value switching
2021-09-24 3DModel: Renders curtain rod
2021-09-28 3DModels: Updates to current versions & documentation
    [EndCap__FreeWheel.f3d, EndCap__FreeWheel.stl, Hanger__Ceiling__End.f3z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]
2021-10-02 Fixes direction switch logic error and adds assignable Mac Address
    [Global.h, Node.ino]
2021-10-02 Adds Nema 17 4023 image
    Since I didn't know different Nema 17s had different wirings
2021-10-04 3DModels: Updates for changes
    [Hanger__Ceiling__Interchange.f3d, Hanger__Ceiling__Interchange.stl, Housing__Driver_ESP32__Cover.f3d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]
2021-10-06 Hub: Updates sample SQL: AdafruitIO: Key: feed_id, Value: position
2021-10-08 Hub: DB sample data defaults to the length of my curtains
2021-11-28 Fixing kinks and listing hardware functionalities
    [Configure.h, Global.h, Node.ino]
2021-11-30 WIP: start work on dual thread for AMT10 encoder
2021-11-30 Node: adds encoder cycling direction calculator
2021-11-30 Node: adds encoder impossible condition logic
2021-11-30 Node: encoder: fixes logic error
    [Encoder.h]
2021-12-19 WIP: Fixed know compile issues (unknown compile issue)
    [Movement.cpp]
2021-12-19 Version compiles Missing JSON creation, movement logic (global Curtain obj, EVent creator)
    [Movement.cpp]
2021-12-21 Movement positioning mostly implemented [COMPILES] Applies the ENDSTOP_PINS as bools for function availability.
2021-12-22 Fixes compile errors & makes movement progress [COMPILES]
    [Movement.cpp]
2021-12-23 Fleshes out specific movements [COMPILES] Movement.hpp needs cleaning up and .cpp needs commenting. Adds additional hardware booleans. Reset and other specific Movement functions remain (as well as e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
    [Movement.cpp]
2022-01-05 Credit to unknown person for belt movement design
2022-02-10 Makes attempt at properly killing threads when leaving scope Reassigning list does not properly call destructor for items in list
2022-02-10 Hub: Updates Thread deletion to prevent thread duplication on System reset
2022-07-09 Makes Hub IP Address adjustable; fixes 2XX issue in curtain event
    [Node.ino]
2022-07-10 Fixes JSON serialization space issues
    [Node.ino]
2022-07-10 Fixes JSON scoping issues
    [Node.ino]
2022-07-10 Removes testing prints
2022-07-10 Fixes logic error in Node; type conversion Hub
    [Node.ino]
2022-07-12 Begins sepparating motor & server
2022-07-13 [COMPILES] Starts moving HTTP server calls to their own thread
2022-07-16 Fixes DB Sample Curtain names
2022-07-16 Fixes loop priority crash & adds docs & tests
    [Node.ino]
2022-07-16 Adds additional test case
2022-07-16 Moves improvements from NodeQueryEncoderless-MotorThread
2022-07-16 Merges simple improvements from NodeQueryEncoderless-MotorThread
2022-07-16 Merges improvements from NodeQueryEncoderless-MotorThread
2022-07-16 Assigns threads to cores
2022-07-17 Fixes changes from Testing
    [Node.ino]
2022-07-17 MotorThread Working Pre-Testing - Cleans up headers - Documents changes - Pulses once
2022-07-17 Starts merging Hub working with MotorThread test
2022-07-17 Adds missing curtain percentage setting functions
    [Movement.cpp]
2022-09-24 Fixes logic/typo errors & add response port
    [Node.ino]
2023-04-02 Makes printing easier for tests
2023-04-14 Completes inserting into view table
2023-05-02 Adds movement sequence diagram & fixes logic error
    [Movement.cpp]
2023-05-03 Adds rendered rod to readme
2023-05-04 Simplifies Threading and continues work on MQTT
2023-05-06 Gets threading changes working
2023-09-23 Updates to track HEAD of SmartCurtain-Backend
2023-09-23 Updates to track HEAD of SmartCurtain-Frontend
2023-09-23 Updates to track HEAD of SmartCurtain-Curtain
2024-01-20 Compiled version that probably does not work
    [Curtain.ino]
2024-01-23 Removes serial prints
2024-01-24 Adjust max length correction; uses UINT32_MAX
    [Movement.cpp]
2024-02-18 Starts fixing bugs found in testing
    [Hardware.cpp, Movement.cpp]
2024-03-15 Fixes static variable issue
    [Curtain.ino]
